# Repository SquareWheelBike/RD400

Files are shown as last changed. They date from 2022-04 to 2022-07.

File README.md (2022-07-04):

# RD400

## Electronics Tray

In the [sketchup](sketchup/) folder, you can find the .stl files for 3d printing the electronics tray. The outlets for wires are modular, so we can swap them out for different types and volumes of wires.

The tray has a top-mounted window, on the lid, so the electronics can be seen inside.

The design for the PCB was crated in EasyEDA.

## The Arduino

The arduino is necessary, since the pushbuttons on the handlebar are momentary push buttons, rather than latching push buttons. Making a latching circuit may have been a trivial affair, but we wanted the ability to expand features in the future. An arduino allows for this kind of modularity.

Arduino code can be viewed in [src/main.ino](src/main.ino).

## NFC

### Recognized Tags

| Tag | Description |
| --- | --- |
| 7A B3 2D 68 | FOB 1 |
| BA 60 22 68 | FOB 2 |
| 95 AB A0 EE | CARD 1 |

### RJ45 PIN MAPPING

| RJ45 | Arduino | MFRNC | Description |
| ---- | --- | ----- | --- |
| 1 | 10 | SDA | SPI SS |
| 2 | 15 | SCK | SPI SCK |
| 3 | 16 | MOSI  | SPI MOSI |
| 4 | 14 | MISO  | SPI MISO |
| 5 | - | RQ | *Unused* |
| 6 | - | GND | *Ground* |
| 7 | 9 | RST | RST |
| 8 | - | Vcc | 2.9V regulated |

### 3.3V Power

The 3.3V for the NFC was actually 2.9V, since the MFRNC522 can run anywhere between 2.5V and 3.3V.

[3V regulation](res/fig1.png)

### Assembly

Electrical assembly notes are under the [res](res/) folder

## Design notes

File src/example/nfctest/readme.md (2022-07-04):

example found [here](https://www.teachmemicro.com/arduino-rfid-rc522-tutorial/)

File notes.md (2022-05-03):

# RD Build-Off Notes

## Post-Build May 1, 2022

### Electronics Enclosure

- The arduino nano *has* to go. this thing keeps having problems. Either move to an embedded ESP for space, or a micro
- The left (output) side output needs to be shifted about an inch outwards
- The FETs need to be more stable. Active low needs to stick around thanks to the bars, but pulldowns and stuff should be prioritized
- On top of the buck converter, voltage protection is a MUST on the arduino. Even if it's just a zener diode stopping the vin from passing a threshold
- The threads need to be shrunk so that the arduino can stay down

### Wiring Harness

- 18awg is NOT enough for the main rail. move to at least 14
- I need a mounted fuse block and preferably a distribution block for power
- the lights and ignition should be fused separately, after the main fuse
- the motogadget M unit is probably the way to stay, NFC will be stinky difficult, unless I wanna put time and ESP resources into it

## May 2, 2022

### What actually failed

- As it turns out, logic-level MOSFETs do not have a very high V<sub>GS</sub>. As a reesult, I burned out the FET gate after extended exposure to 12V. Although V<sub>DS</sub> is 60V, we need to maintain a low V<sub>GS</sub>.
- Somehow, an 18awg wire burned, drawing 2.5 amps.
- The 18awg has been replaced by 12awg for the main battery wire
- The motogadget will not stay on, even with no load on the system. It MAY need a backing capacitor

keith z

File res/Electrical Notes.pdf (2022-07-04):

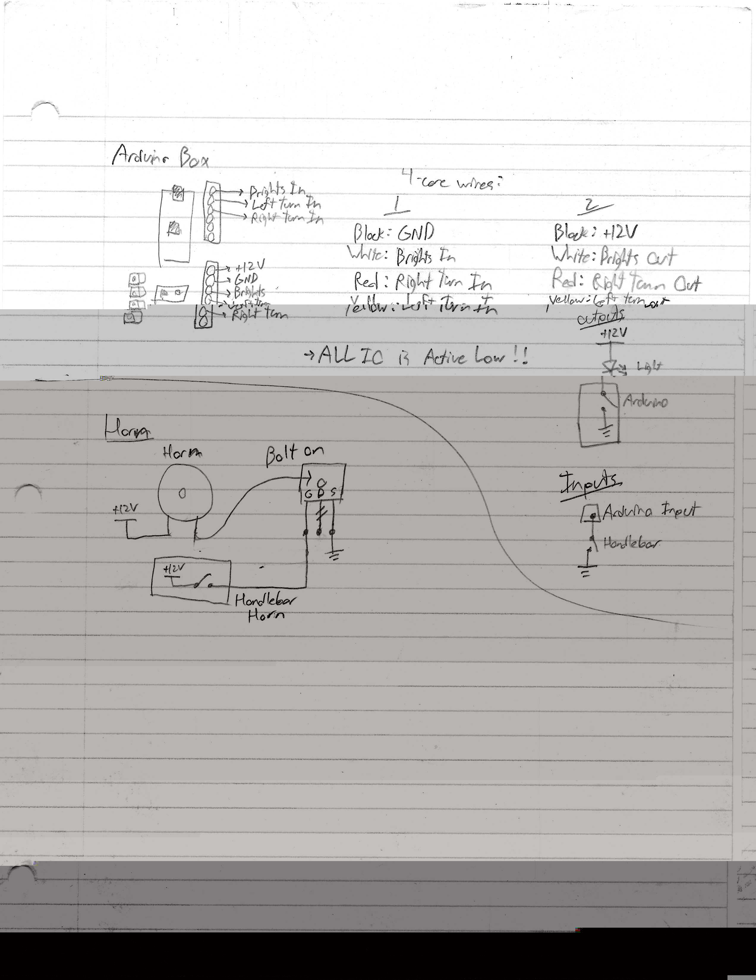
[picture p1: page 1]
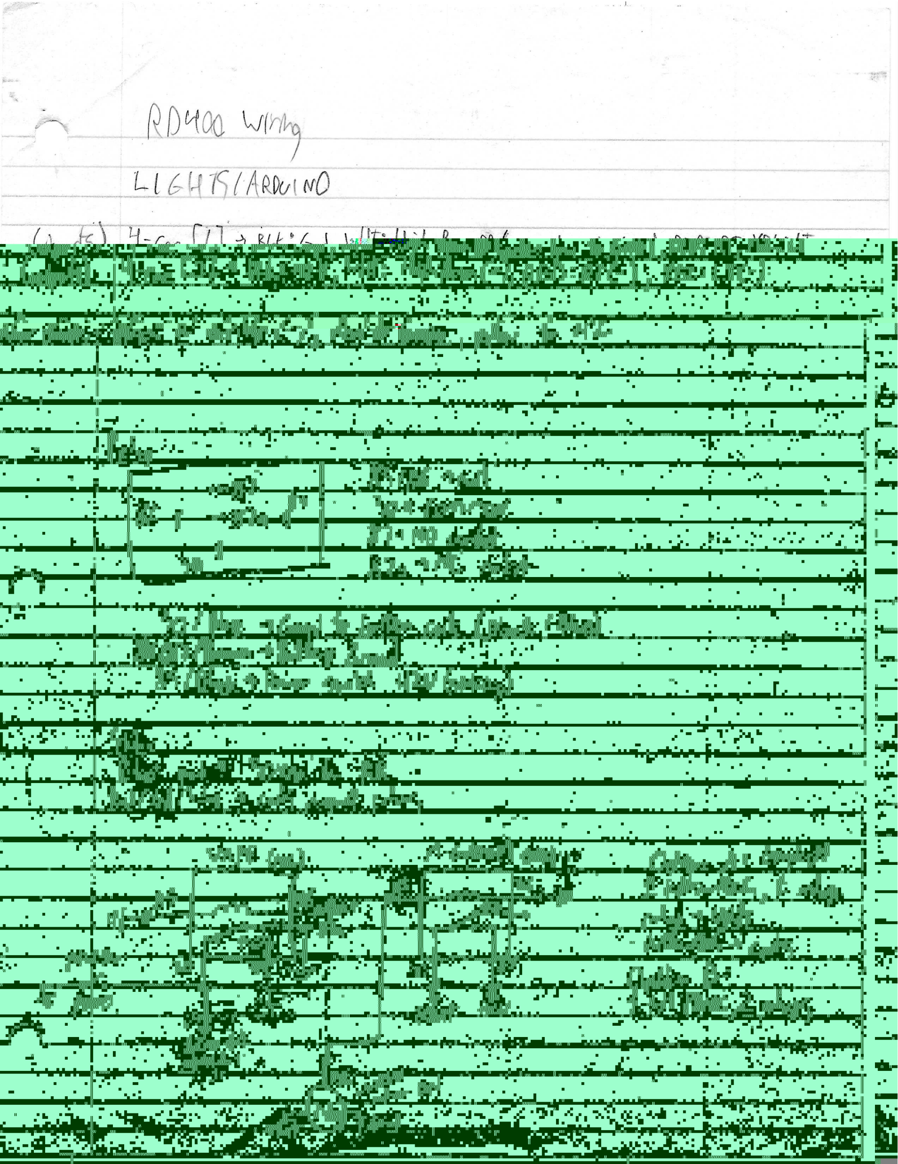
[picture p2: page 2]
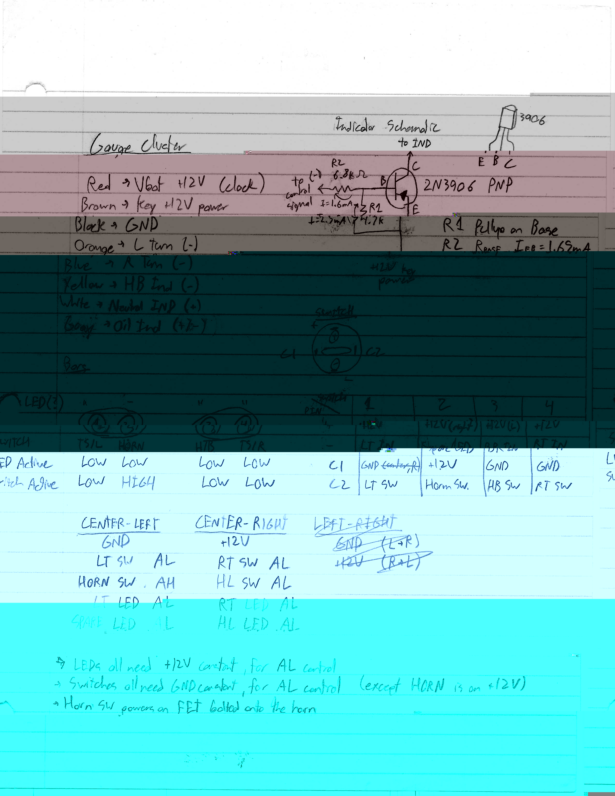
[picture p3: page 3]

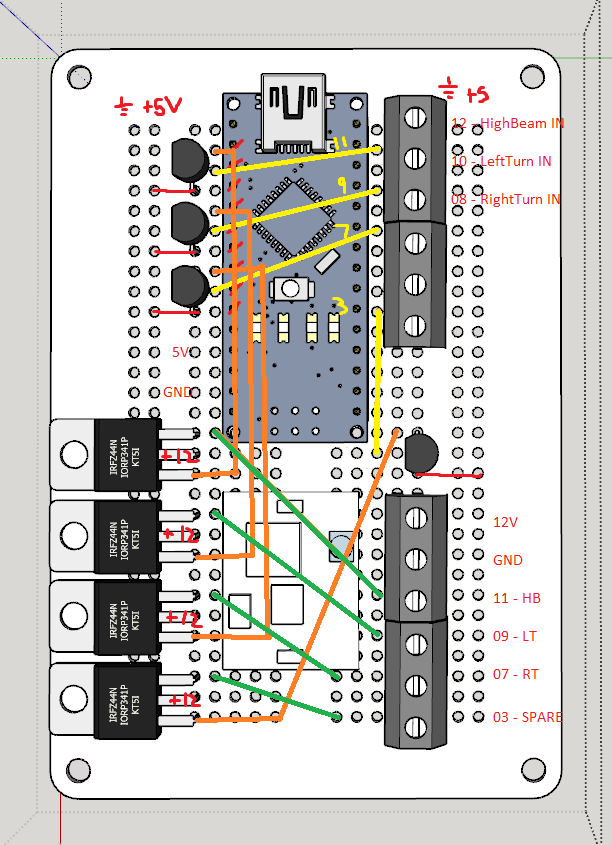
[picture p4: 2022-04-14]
pinout.png

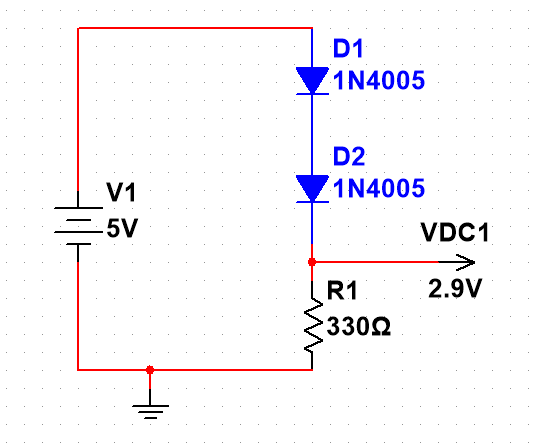
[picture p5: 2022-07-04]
res/fig1.png

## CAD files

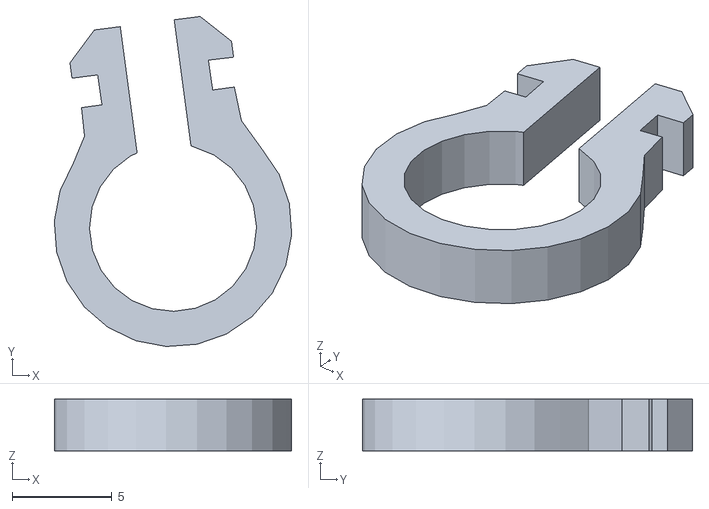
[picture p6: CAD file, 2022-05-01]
sketchup/clips/0.2in hole 1.5 deep.stl
11.9 x 16.5 x 2.59

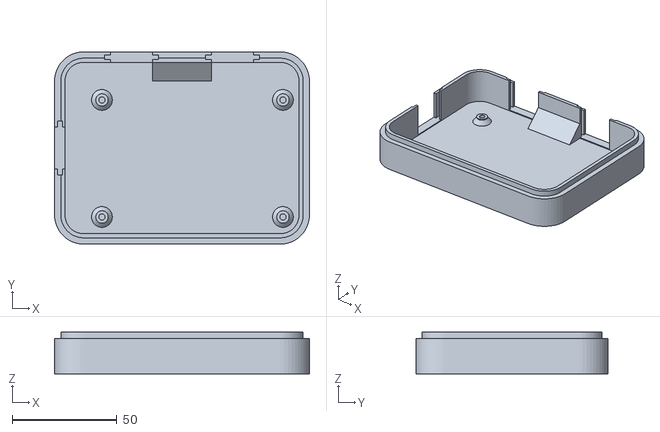
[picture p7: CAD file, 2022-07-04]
sketchup/enclosure/tray.stl
122.0 x 92.0 x 20.0

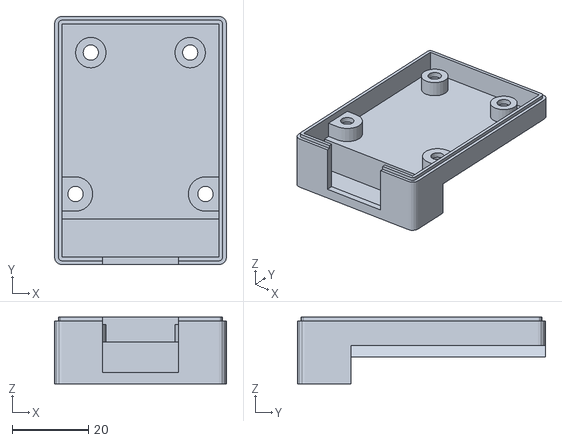
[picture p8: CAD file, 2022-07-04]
sketchup/nfc/tray.stl
45.0 x 65.0 x 17.5

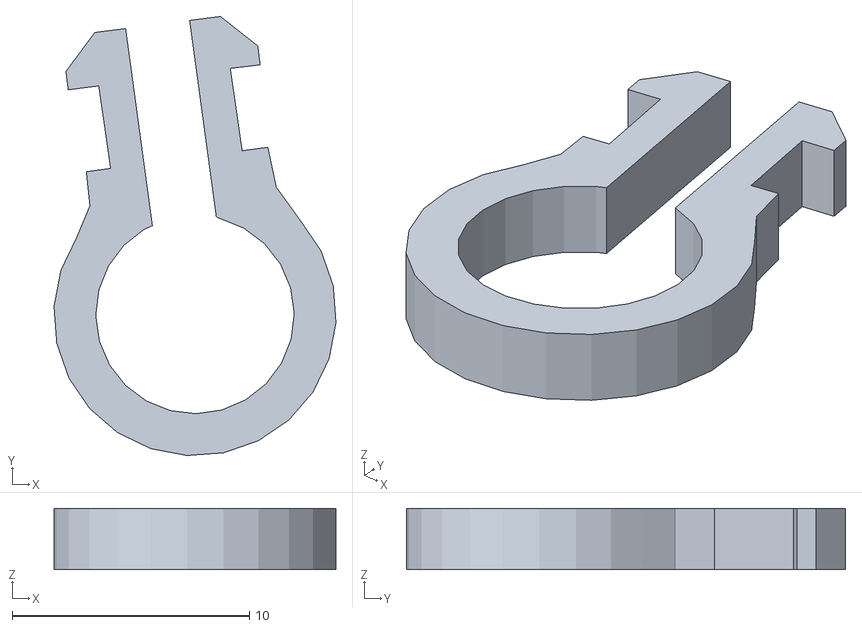
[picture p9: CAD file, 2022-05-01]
sketchup/clips/0.2in hole 3.5 deep.stl
11.9 x 18.5 x 2.59

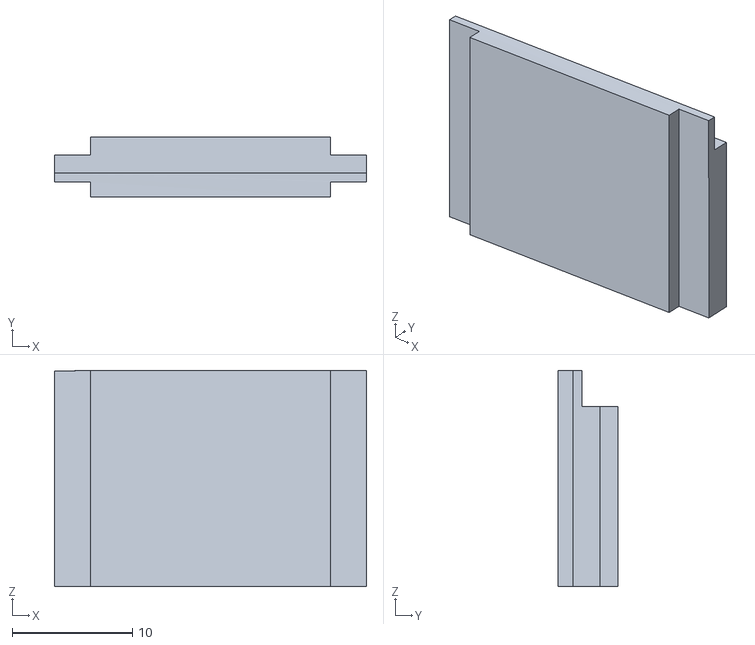
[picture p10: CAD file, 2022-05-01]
sketchup/enclosure/block insert.stl
26.0 x 5.00 x 18.0

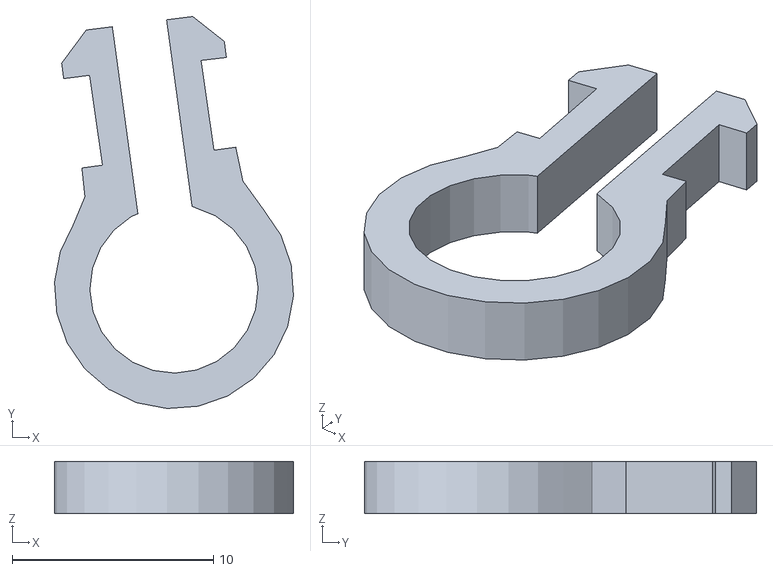
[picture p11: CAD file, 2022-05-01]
sketchup/clips/0.2in hole 4.5 deep.stl
11.9 x 19.5 x 2.59

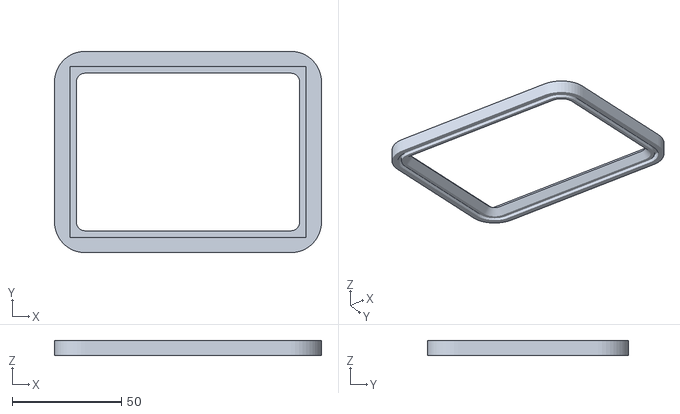
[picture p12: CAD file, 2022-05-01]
sketchup/enclosure/lid.stl
122.0 x 92.0 x 6.67

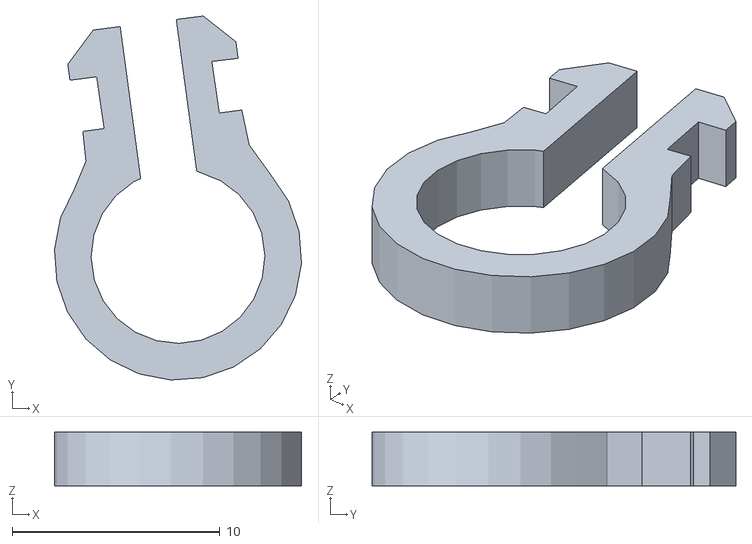
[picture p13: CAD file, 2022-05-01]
sketchup/clips/0.2in hole 2.5 deep.stl
11.9 x 17.5 x 2.59

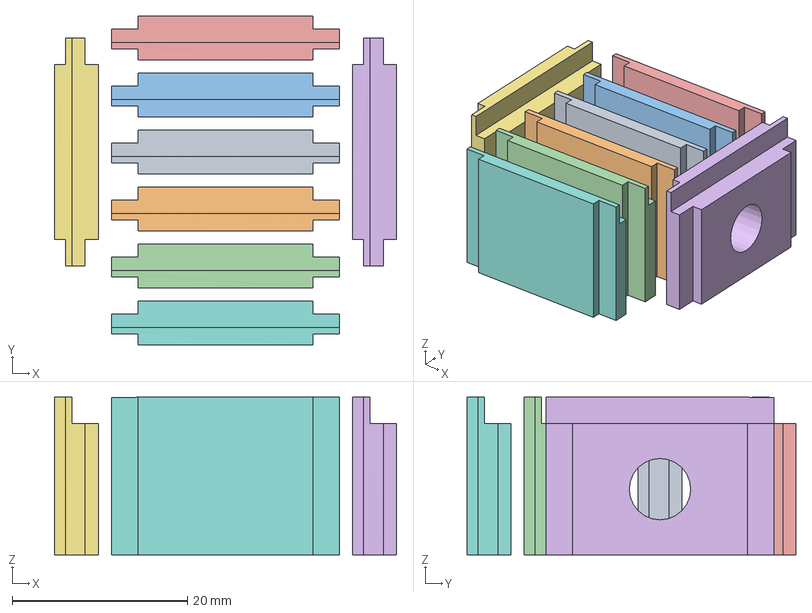
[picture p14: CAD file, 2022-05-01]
sketchup/enclosure/CE3_5mm insert.3mf
39.0 x 37.5 x 18.0 mm
5mm insert.stl
block insert.stl
7mm insert.stl
10mm insert.stl
5mm insert.stl(1)
7mm insert.stl(1)
10mm insert.stl(1)
block insert.stl(1)

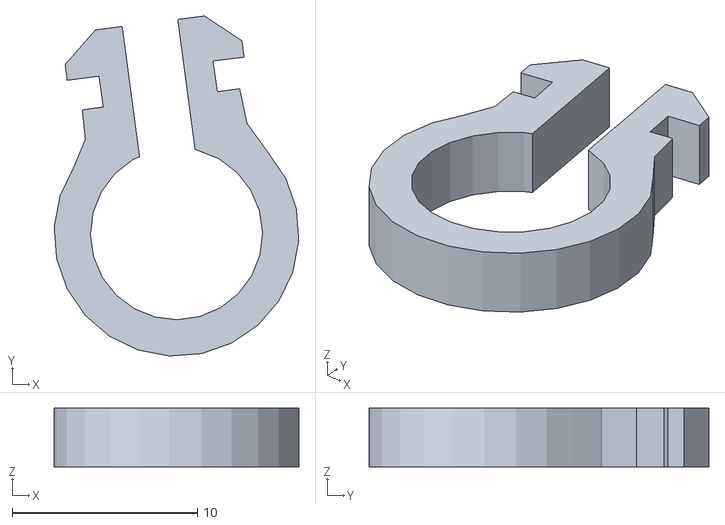
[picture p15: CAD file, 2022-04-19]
sketchup/clips/0.25in hole.stl
13.2 x 18.4 x 3.16

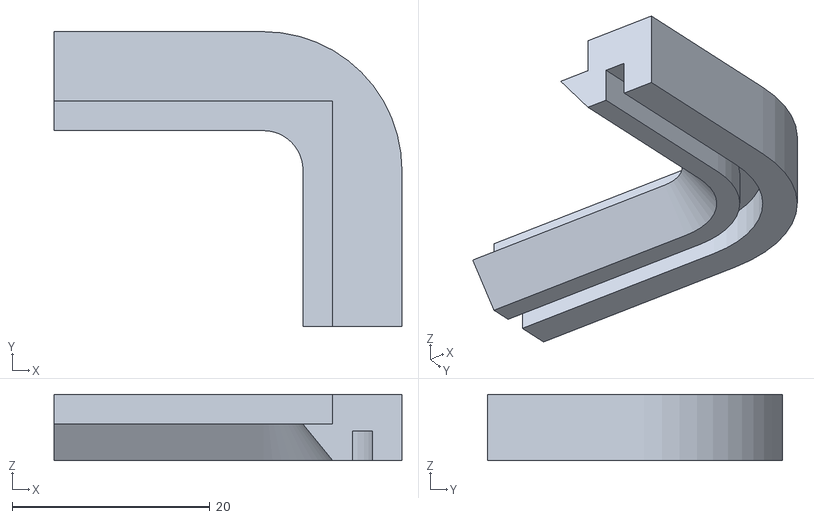
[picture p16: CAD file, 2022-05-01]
sketchup/enclosure/lid_test.stl
35.2 x 29.8 x 6.67

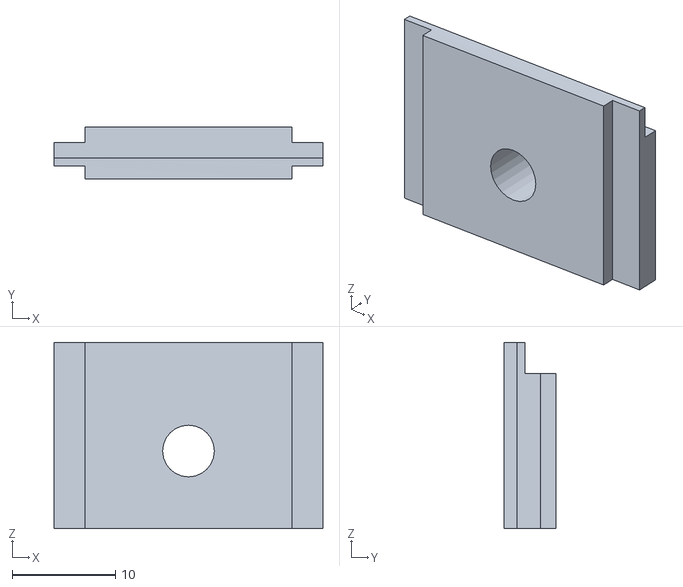
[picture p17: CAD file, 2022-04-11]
sketchup/enclosure/5mm insert.stl
26.0 x 5.00 x 18.0

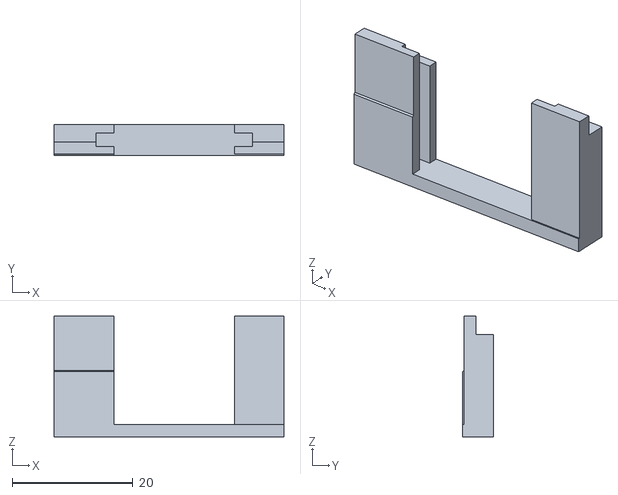
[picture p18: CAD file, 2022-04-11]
sketchup/enclosure/test.stl
38.2 x 5.09 x 20.0

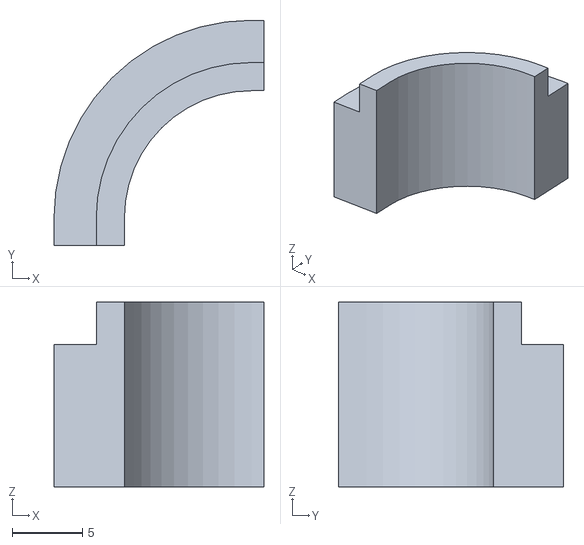
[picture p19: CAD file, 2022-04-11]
sketchup/enclosure/testbottom.stl
14.9 x 16.0 x 13.1

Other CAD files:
sketchup/enclosure/10mm insert.stl
sketchup/enclosure/7mm insert.stl
sketchup/enclosure/testlid.stl
sketchup/clips/WireClipSizes.skp
sketchup/enclosure.skp

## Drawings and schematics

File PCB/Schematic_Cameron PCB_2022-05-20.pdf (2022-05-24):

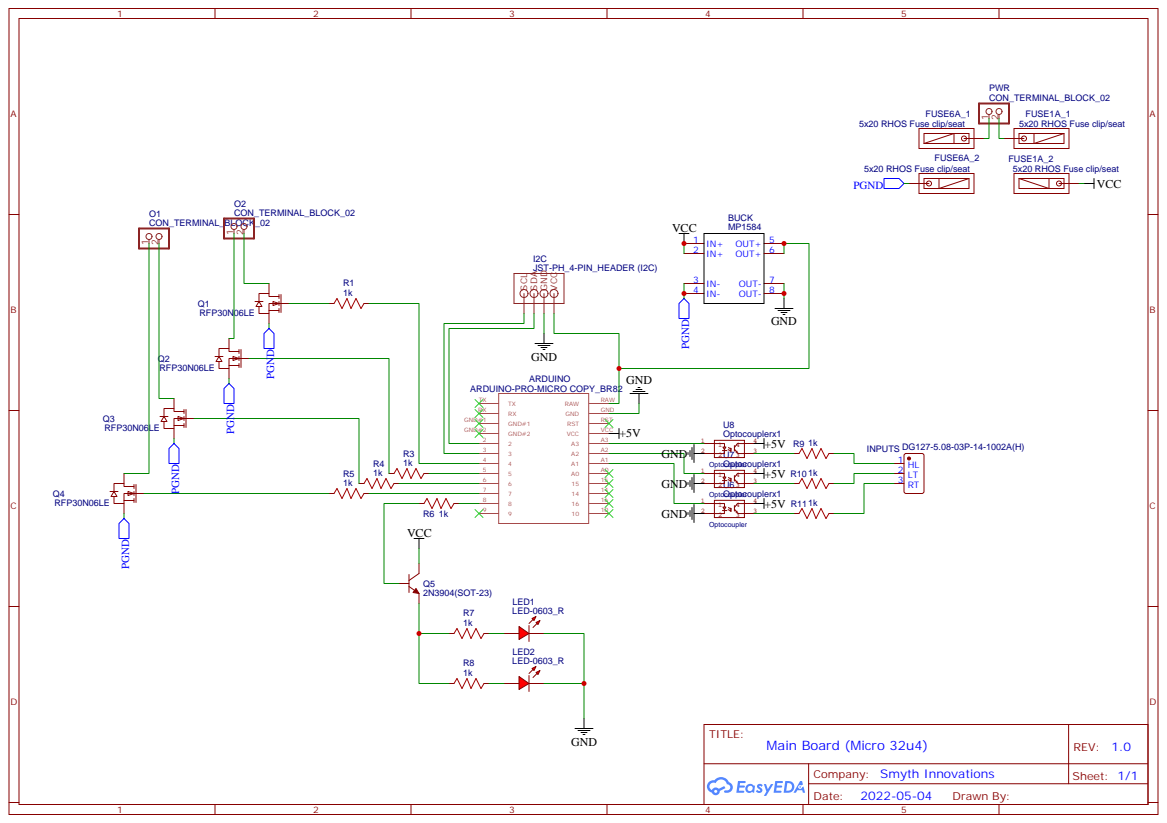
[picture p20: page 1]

FUSE1A_1
5x20 RHOS Fuse clip/seat

FUSE1A_2

PGND

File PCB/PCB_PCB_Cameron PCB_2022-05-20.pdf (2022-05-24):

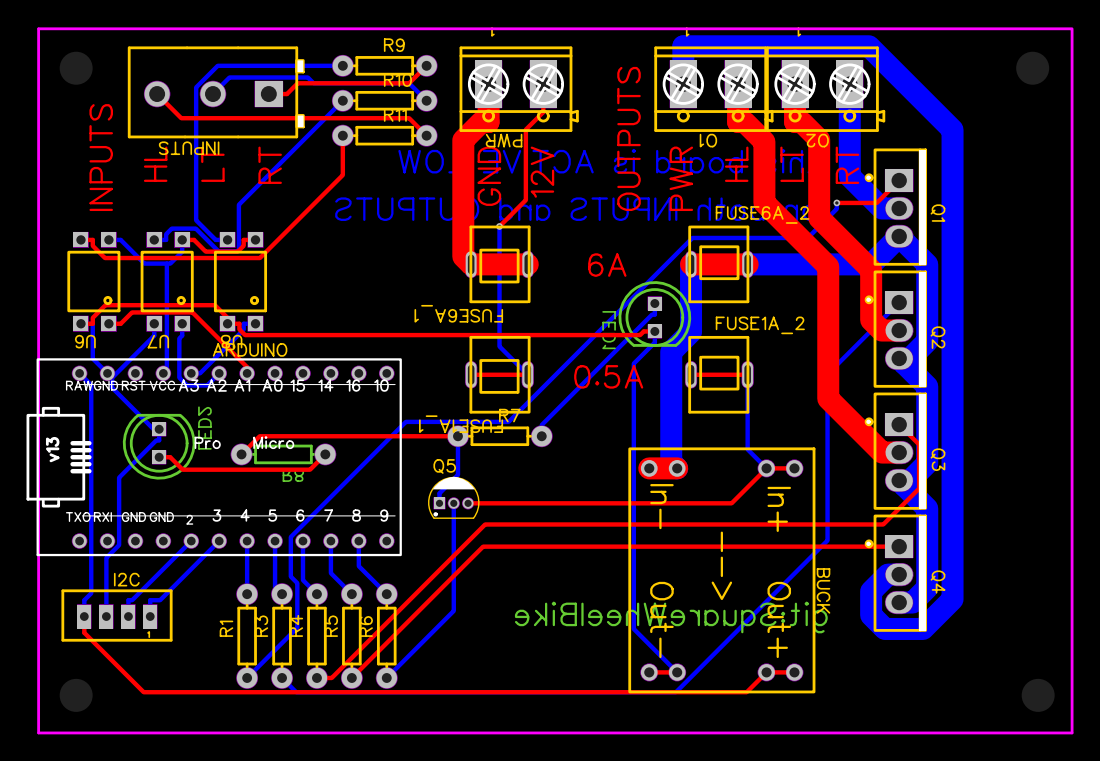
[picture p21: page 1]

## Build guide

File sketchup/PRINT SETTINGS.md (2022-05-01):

# Print Settings

IMPORTANT, since each part has fairly tight tolerances

These settings relate to horizontal expansion tuning in UltiMaker Cura.

## PLA

Inserts:

- horizontal expansion -0.07mm
- initial layer expansion -0.1mm
- hole expansion 0mm

Everything Else:

- horizontal expansion -0.05mm
- initial layer expansion -0.08mm
- hole expansion 0mm

Lid (ABS):

- horizontal expansion -0.25mm
- initial layer expansion -0.25mm

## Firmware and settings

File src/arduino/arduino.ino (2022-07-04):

/**
 * @file arduino.ino
 * @author cole fuerth
 * @brief debounced input pullups for inputs, and toggleable outputs
 * @version 0.2
 * @date 2022-04-14
 *
 * @copyright Copyright (c) 2022
 *
 */

// toggle debug mode (define before including rd400.h)
#define __DEBUG
#include "rd400.h"
#include <SPI.h>
#include <MFRC522.h>

#define BRIGHTS_IN A1
#define BRIGHTS_OUT 6
#define LT_IN A2
#define LT_OUT 5
#define RT_IN A3
#define RT_OUT 4
#define UNDERGLOW_OUT 8

#define SDA 2
#define SCL 3
#define POWER_OUT 7 // main power
#define RST_PIN 9   // arbitrary, can be any GPIO pin
#define SS_PIN 10   // also arbitrary

BRIGHTS brights(BRIGHTS_OUT, new TOGGLE_BUTTON(BRIGHTS_IN));
TURNSIGNAL lt(LT_OUT, new TOGGLE_BUTTON(LT_IN));
TURNSIGNAL rt(RT_OUT, new TOGGLE_BUTTON(RT_IN));

IO *io_list[] = {&brights, &lt, &rt};

MFRC522 rfid(SS_PIN, RST_PIN); // Create MFRC522 instance.
// registered cards, hard coded for now
const byte uids[3][4] = {
    {0x7A, 0xB3, 0x2D, 0x68},
    {0xBA, 0x60, 0x22, 0x68},
    {0x95, 0xAB, 0xA0, 0xEE}};

void setup()
{
#ifdef __DEBUG
    Serial.begin(9600);
    for (unsigned long stime = millis(); !Serial && (millis() - stime) < 2000; delay(1))
        ;
#endif
    // initialize pinModes (not set when constructing above objects)
    for (auto i : io_list)
    {
        pinMode(i->pin, OUTPUT);
        DEBUGLN("pin " + String(i->pin) + " output");
        pinMode(i->control->pin, INPUT_PULLUP);
        DEBUGLN("pin " + String(i->control->pin) + " input");
    }

    // underglow control pin is on all the time for now
    pinMode(UNDERGLOW_OUT, OUTPUT);
    digitalWrite(UNDERGLOW_OUT, HIGH);

    // initialize power output to be always HIGH
    pinMode(POWER_OUT, OUTPUT);
    digitalWrite(POWER_OUT, LOW);

    DEBUGLN(F("Starting SPI"));
    SPI.begin();
    DEBUGLN(F("Initializing MFRC522"));
    rfid.PCD_Init();
    if (rfid.PCD_PerformSelfTest())
        DEBUGLN(F("NFC Passed Self-Test"));

    DEBUGLN("setup complete");
}

void loop()
{
    for (auto i : io_list)
    {
        i->update_state();
    }

    // NOTE: this will break things if it is not at the END of loop()
    switch (checkNFC())
    {
    case 0:
        break;
    case -1:
        DEBUG(F("Unrecognized card detected "));
        printHex(rfid.uid.uidByte, rfid.uid.size);
        DEBUGLN();
        break;
    default:
        DEBUG(F("Card detected "));
        printHex(rfid.uid.uidByte, rfid.uid.size);
        DEBUGLN();
        digitalWrite(POWER_OUT, !digitalRead(POWER_OUT)); // toggle power
        rfid.PICC_HaltA();
        rfid.PCD_StopCrypto1();
        break;
    }
    delay(1);
}

// ----------------- NFC FUNCTIONS -----------------

void printHex(byte *buffer, byte bufferSize)
{
    for (byte i = 0; i < bufferSize; i++)
    {
        DEBUG(buffer[i] < 0x10 ? " 0" : " ");
        DEBUG(String(buffer[i], HEX));
    }
}

/**
 * @brief Check for NFC card available, and return whether the card is recognized or not.
 *
 * @return int 1 if card is recognized, 0 if card is not found, -1 if card is unrecognized.
 */
int checkNFC()
{
    // check if a card is available
    if (!rfid.PICC_IsNewCardPresent() || !rfid.PICC_ReadCardSerial())
        return 0;

    // this is a bit of a hack, but it works.
    bool found = false;
    for (int u = 0; u < 3; u++)
    {
        byte *uid = uids[u];
        found = true;
        for (byte i = 0; i < 4; i++)
        {
            if (uid[i] != rfid.uid.uidByte[i])
            {
                found = false;
                break;
            }
        }
        if (found)
            return 1;
    }
    return -1;
}

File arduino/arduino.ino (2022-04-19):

/**
 * @file arduino.ino
 * @author cole fuerth
 * @brief debounced input pullups for inputs, and toggleable outputs
 * @version 0.1
 * @date 2022-04-14
 *
 * @copyright Copyright (c) 2022
 *
 */

#define __NANO

#ifdef __NANO

#define BRIGHTS_IN 12
#define BRIGHTS_OUT 5
#define LT_IN 10
#define LT_OUT 11
#define RT_IN 8
#define RT_OUT 9
#define UNDERGLOW_OUT 3

#define SPARE1_IN 6
#define SPARE2_IN 4
#define SPARE3_IN 2
#define SPARE1_OUT 7

#else

#define BRIGHTS_IN 9
#define BRIGHTS_OUT 8
#define LT_IN 7
#define LT_OUT 6
#define RT_IN 5
#define RT_OUT 4
#define UNDERGLOW_OUT 3

#endif

/**
 * @brief debounced INPUT_PULLUP on a pin; produces a state for outputs to use
 *
 */
class TOGGLE_BUTTON
{
public:
    bool state, input;
    uint8_t pin;
    uint16_t debounce;

    TOGGLE_BUTTON(uint8_t pin, uint16_t debounce_delay = 20)
    {
        this->pin = pin;
        this->debounce = debounce_delay;
        this->state = 0;
        this->input = 0;
    }

    boolean update_state()
    {
        if (oneShot(debounce_func(!digitalRead(pin))))
        {
            state = !state;
        }
        return state;
    }

private:
    boolean OSB, timerInSession, timerMemory;
    unsigned long timerTimer;

    boolean debounce_func(boolean in)
    {
        if (TON(in != input, debounce))
        {
            input = in;
            // Serial.println("pin " + String(pin) + " input " + String(input ? "HIGH" : "LOW"));
        }
        return input;
    }

    boolean oneShot(boolean precond)
    {
        // use global memory to keep track of oneshot bits
        if (precond == 1 && this->OSB == 0)
        {
            this->OSB = 1;
            return 1;
        }
        else if (precond == 0 && this->OSB == 1)
        {
            this->OSB = 0;
            return 0;
        }
        else
            return 0;
    }

    boolean TON(boolean input, int preset)
    {
        if (input && !timerInSession)
            timerTimer = millis();
        else if (input && timerMemory)
            return 1;
        else if (input && millis() - timerTimer >= preset)
        {
            timerMemory = 1;
            return 1;
        }
        else
            ;
        timerMemory = 0;
        timerInSession = input;
        return 0;
    }
};

class IO
{
public:
    TOGGLE_BUTTON *control;
    uint8_t pin;
    IO() {}
    ~IO() { delete control; }
    virtual boolean update_state();
};

class BRIGHTS : public IO
{
public:
    /**
     * @brief Construct a new BRIGHTS object
     *
     * @param pin output pin
     * @param input TOGGLE_BUTTON constructed with `new`
     */
    BRIGHTS(uint8_t pin, TOGGLE_BUTTON *input)
    {
        this->pin = pin;
        this->control = input;
    }

    boolean update_state()
    {
        digitalWrite(pin, control->update_state());
    }
};

class TURNSIGNAL : public IO
{
public:
    float hz;

    TURNSIGNAL(uint8_t pin, TOGGLE_BUTTON *input, float hz = 1)
    {
        this->pin = pin;
        this->control = input;
        this->hz = hz;
    }

    boolean update_state()
    {
        digitalWrite(pin, control->update_state() && FlasherBit(hz));
    }

private:
    boolean FlasherBit(float hz)
    {
        int T = round(1000.0 / hz);
        if (millis() % T >= T / 2)
            return 1;
        else
            return 0;
    }
};

BRIGHTS brights(BRIGHTS_OUT, new TOGGLE_BUTTON(BRIGHTS_IN));
TURNSIGNAL lt(LT_OUT, new TOGGLE_BUTTON(LT_IN));
TURNSIGNAL rt(RT_OUT, new TOGGLE_BUTTON(RT_IN));

IO *io_list[] = {&brights, &lt, &rt};

void setup()
{
    // Serial.begin(115200);
    // while (!Serial)
    //     delay(1);
    // initialize pinModes (not set when constructing above objects)
    for (auto i : io_list)
    {
        pinMode(i->pin, OUTPUT);
        // Serial.println("pin " + String(i->pin) + " output");
        pinMode(i->control->pin, INPUT_PULLUP);
        // Serial.println("pin " + String(i->control->pin) + " input");
    }

    // underglow control pin is on all the time for now
    pinMode(UNDERGLOW_OUT, OUTPUT);
    digitalWrite(UNDERGLOW_OUT, HIGH);

// initialize spares
#ifdef __NANO
    pinMode(SPARE1_OUT, OUTPUT);
    digitalWrite(SPARE1_OUT, LOW);
    pinMode(SPARE1_IN, INPUT_PULLUP);
    pinMode(SPARE2_IN, INPUT_PULLUP);
    pinMode(SPARE3_IN, INPUT_PULLUP);
#endif

    // Serial.println("setup complete");
}

void loop()
{
    for (auto i : io_list)
    {
        i->update_state();
    }
    delay(1);
}

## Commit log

2022-04-11 tray print ready
    [enclosure.skp, tray.stl]
2022-04-13 arduino initial program revision
2022-04-13 stls updated
    [10mm insert.stl, 5mm insert.stl, 7mm insert.stl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]
2022-04-14 enclosure drawing updated
    [enclosure.skp]
2022-04-14 drawing changes
    [enclosure.skp]
2022-04-19 fet datasheet
2022-04-19 wire clips
    [0.25in hole.stl]
2022-05-13 esp started
    [WireClipSizes.skp]
2022-05-24 board design done
    [CE3_5mm insert.3mf]
2022-06-27 temp power always high
2022-07-03 rename schematics folder with no whitespace
2022-07-04 nfc enclosure designed
    [enclosure.skp, tray.stl]
2022-07-04 added 3v regulation schematic
2022-07-04 reorganize sketchup folder
    [10mm insert.stl, 5mm insert.stl, 7mm insert.stl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]
